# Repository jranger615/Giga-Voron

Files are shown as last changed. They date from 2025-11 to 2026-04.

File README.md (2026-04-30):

# Giga-Voron

#### 4-25-2026 - adding LOW version of my Adapter, this lowers the mount by 10mm (Raises the voron), which should allow for use of the stock connection cable. I HAVE not tested it out but it should work fine, just make sure to keep your stock stepper Z min position if you use it. 

## Things you may want to buy
* To save some assembly steps and the need for buy tons of screws you can by a fully assembled stealth burner. It will require dissassembly to attach to the new mounts and replace board/wiring
https://www.formbot3d.com/products/stealthburner-extruder-for-troodon-20?VariantsId=11006
* The stock board uses  ZH1.5 Connectors, you can buy connector packs on amazon, for ease of use, i buy the pre-crimped ones as they are tiny.
* 2510 24v Fan (Optional for Extruder Board Cooling)
* Longer Cable for the CAN  XT30 2+2. I extended mine but also made a new model of the mount to raise it up for the stock use. Will need to adjust your Z if you do this
* Some M3 screws for assembly (Various sizes for the LID, LID Fan, and Installing the board and adapter
  
## Things to Print
* Your StealthBurner and Prefered Hot End Assembly (If you dont buy and dissasemble formbot)
* The Adapter of Choice from the STL Folder (Beacon or Stock Sensor) I have no started the beacon config yet)
* Board Adapter, this allows you to install the stock board on the Voron
* LID of Choice, Standard or FAN LID. This is different then stock stealth burner to accommodate the stock board install 

## ASSEMBLY Notes
* You will have to open up the top holes on the adapter a little or just work your M3 screws through them before install on the stealth burner.
* Light and Stock sensor are very tight fit. Install them before your stealthburner
* Screws will be longer then the stock mount screws. Make sure you dont get them too long or the mount might not sit flush

## Stealthburner
Assemble the VORON Stealthburner if you dindt buy the formBot. Remember we use a different LID and Board Adapter.
* Follow the build guide located here. This is a large step, and your toolhead will only function as well as you assemble it, so take your time.
* this video is also helpful https://youtu.be/dOyYvnehLaI?si=HIRMF422sOZMZnhB

## Board Diagram and Adapter Mount
  The board Adapter attaches with 2 M3 screws and the stock board requires a m3 screw and washer to hold secure.
  * Attach all wires before sliding the board into place. Itsa tight fit and goes in on an angle.
  * There is an allighment pin on the right next to the nut cert, this helps keep the board in place when the 1 bolt is installed
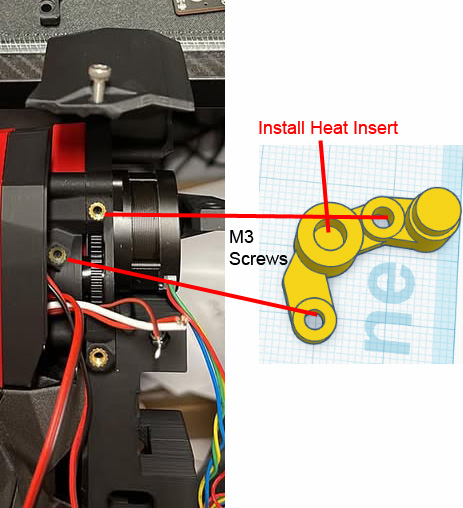
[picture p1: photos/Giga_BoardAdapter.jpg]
  * 
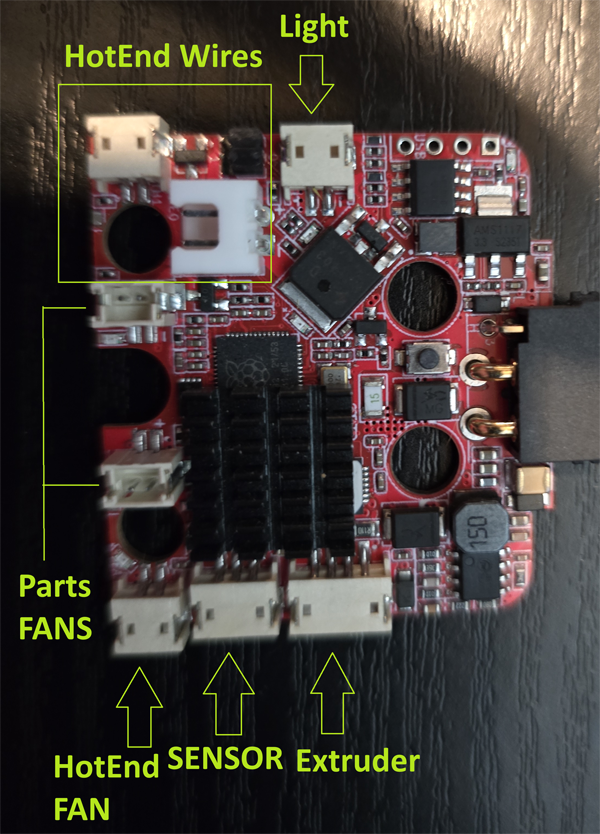
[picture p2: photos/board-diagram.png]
  * 

## Adapter StealthBurner Mount Assembly
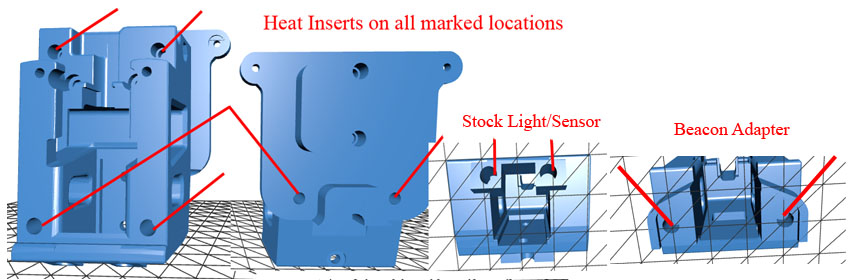
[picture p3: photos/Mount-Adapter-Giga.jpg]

  
## FormBot Moons Stepper Motor Wiring Ref:
* Blue >  Blue (On Stock Connector)
* Red > Red (On Stock Connector)
* Orange > Black (On Stock Connector)
* Black > Green (On Stock Connector)

## Fans:
You can use the Stock Fans from the Giga 
* Bottom fan wire will need to be extended.
* Top Fan, you will have to split the casing apart to fit in the Voron
* Optional 2510 Fan for the Board Cooling Funtion

## Can Bus Wiring XT30 2+2
*  Can Low - Green
*  Can High - Black
*  24V - Red
*  Ground - White

# PRINTER.CFG CHANGES
Y Offset changes everywhere to +15 to accomdate the size of the VORON

## In Probe Offsets
  ```ruby
y_offset: 16
x_offset: 0
z_offset: 10.0      # ← Add +10 (or start with +9.5 and fine-tune)
 ```

## In [stepper_y]
```ruby
 position_min: 29  # Nozzle was more forward then stock and the case was 15 mm bigger. After testing 29 brings the nozzle to the front 
 ```

## In [bed_mesh]
```ruby
 mesh_min:10,45
 ```

## In [gcode_macro CANCEL_PRINT]
  ```ruby
{% set y_park = params.Y|default(printer.toolhead.axis_minimum.y + 45)|int %}   # changed +30 → +45
 ```

## In [gcode_macro PAUSE]
  ```ruby
{% set y_park = params.Y|default(printer.toolhead.axis_minimum.y + 45)|int %}   # changed +30 → +45
 ```

## In [homing_override]
  ```ruby
    {% set y_park = 218 | float %}     # was 203 → add +15
 ```

## In [stepper_z]
  ```ruby
position_min: -22      # ← Change from -12 to -22 (gives more negative room)
 ```

## In [stepper_x]
  ```ruby
position_min: -1     # ← Change from -5 to -1 Position the nozzle at edge 
 ```

## in PLR.CFG
  ```ruby
[delayed_gcode KINEMATIC_POSITION]
initial_duration:0.2
gcode:
      SET_KINEMATIC_POSITION X=0
      SET_KINEMATIC_POSITION Y=25 #Changed from 0 to make sure we dont crash into the front
      SET_KINEMATIC_POSITION Z=0
 ```

## In znp_thr1.cfg (Which ever port you use for yours)
* gear_ratio: 50:10
* rotation_distance: 22.635 #This needs to be adjusted and Calibrated to youyr machine.  Stock start point 22.68 
* sensor_type: ATC Semitec 104NT-4-R025H42G # Change to match Sensor

## Orca Slicer Changes (Specific to Bambu Labs X1C Hotend)
* In the Machine Settings, Set Extruder 1, Retraction length to 1.1
* Layer Heights Limits, Set Max to .48

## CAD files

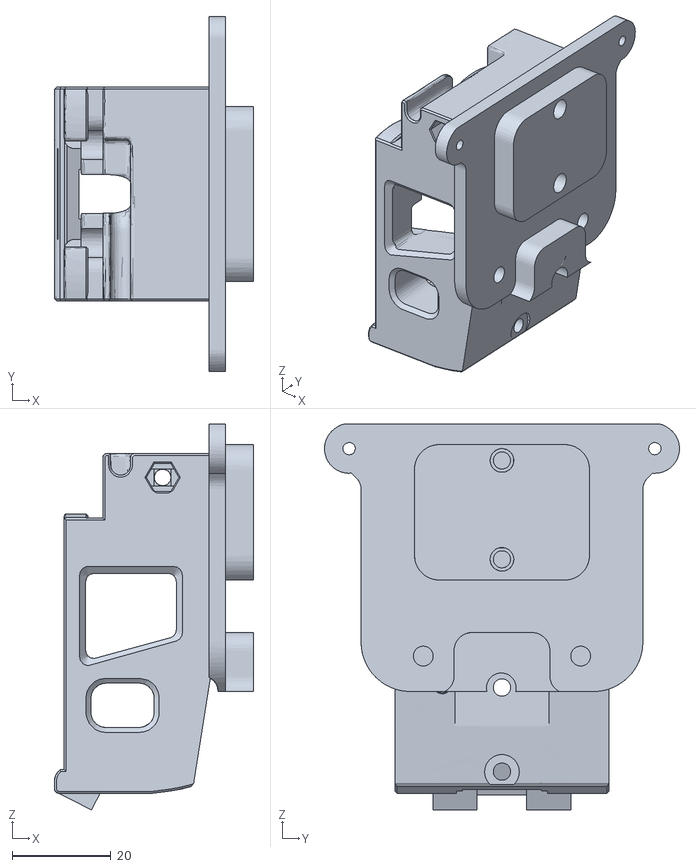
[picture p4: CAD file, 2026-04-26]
STLs/LOW-Giga Voron Stock Adapter.stl
40.3 x 71.8 x 78.1

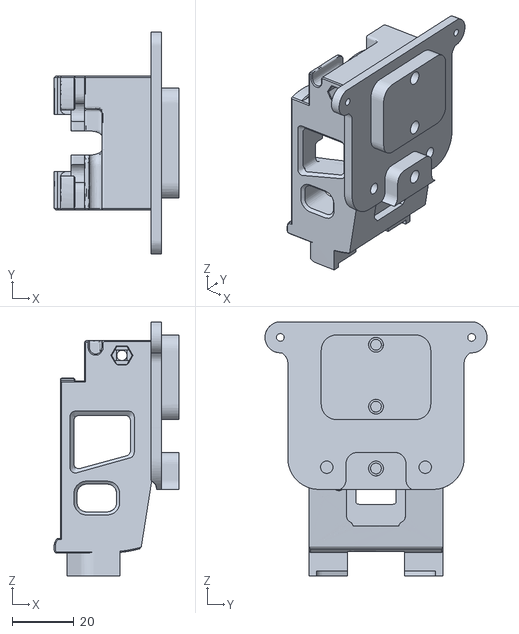
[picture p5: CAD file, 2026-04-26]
STLs/LOW-Giga Voron Beacon Adapter.stl
40.3 x 71.8 x 82.1

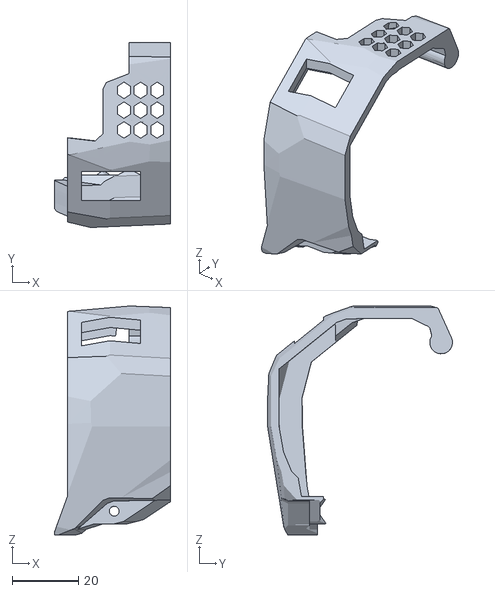
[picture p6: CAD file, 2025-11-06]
STLs/Giga Voron Lid.stl
35.2 x 56.1 x 69.4

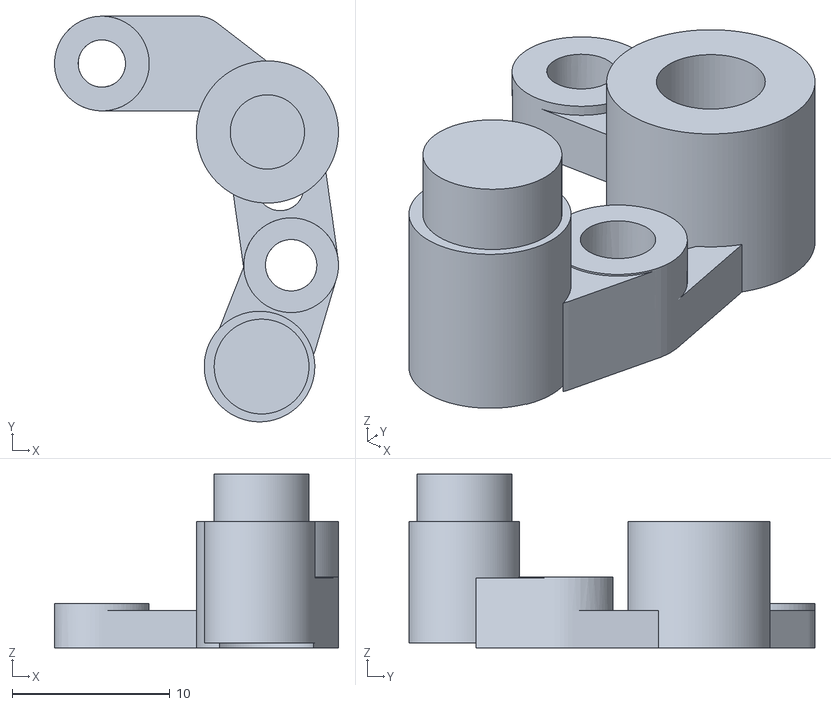
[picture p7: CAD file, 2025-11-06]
STLs/Giga Voron Board Adapter.stl
18.0 x 25.7 x 11.0

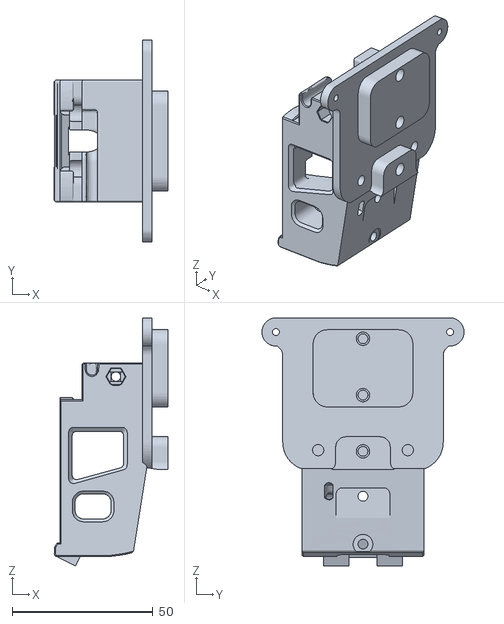
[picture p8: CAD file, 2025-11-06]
STLs/Giga Voron Stock Sensor Adapter.stl
40.3 x 71.8 x 88.1

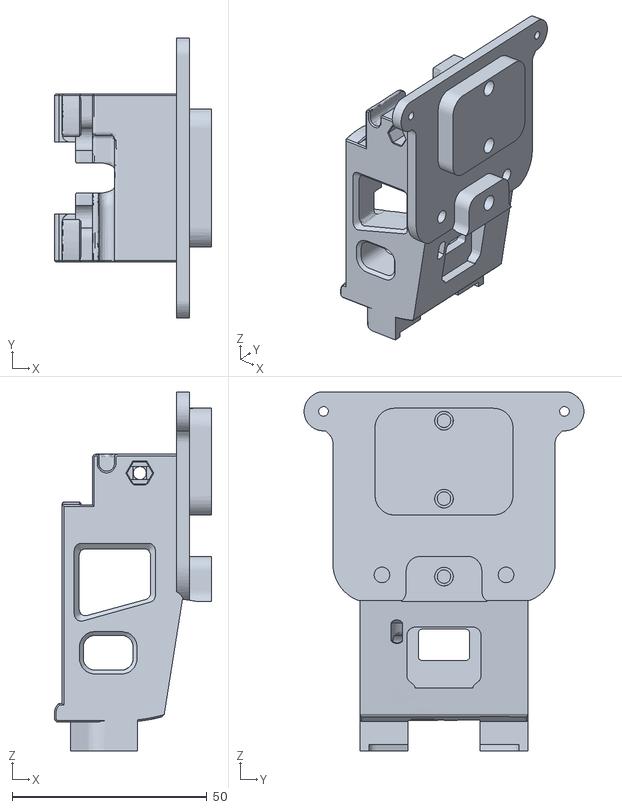
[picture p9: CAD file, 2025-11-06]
STLs/Giga Voron Beacon Adapter.stl
40.3 x 71.8 x 92.1

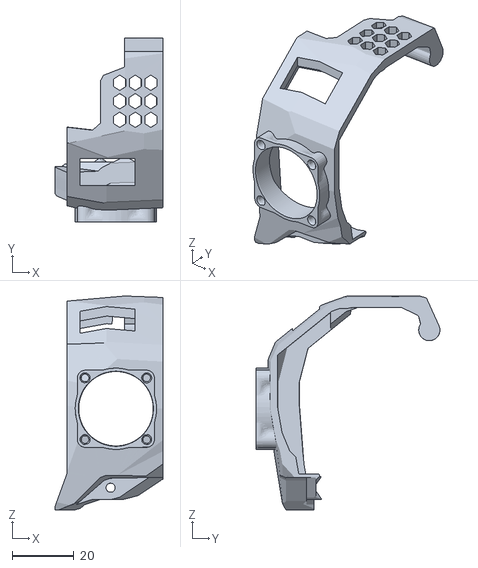
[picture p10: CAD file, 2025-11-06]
STLs/Giga Voron Fan Lid.stl
35.2 x 59.6 x 69.4

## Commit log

2025-11-06 Rename Giga Voron Beacon Adapter.stl to STLs/Giga Voron Beacon Adapter.stl
    [Giga Voron Beacon Adapter.stl]
2025-11-06 Rename Giga Voron Board Adapter.stl to STLs/Giga Voron Board Adapter.stl
    [Giga Voron Board Adapter.stl]
2025-11-06 Rename Giga Voron Fan Lid.stl to STLs/Giga Voron Fan Lid.stl
    [Giga Voron Fan Lid.stl]
2025-11-06 Rename Giga Voron Lid.stl to STLs/Giga Voron Lid.stl
    [Giga Voron Lid.stl]
2025-11-06 Rename Giga Voron Stock Sensor Adapter.stl to STLs/Giga Voron Stock Sensor Adapter.stl
    [Giga Voron Stock Sensor Adapter.stl]
2026-04-22 Update README with assembly and wiring instructions
    Added detailed instructions for assembly and wiring of the stealth burner and fans.
2026-04-23 Update README with connector and wiring details
    Added information about ZH1.5 connectors and wiring for stepper motors.
2026-04-23 Update README with fan and connector details
2026-04-25 Update Can Bus Wiring section title in README
2026-04-25 Add probe offsets section to README
2026-04-25 Add stepper_y section to README
2026-04-25 Fix formatting in README.md for stepper_y and bed_mesh
2026-04-25 Update README with cooling fan configuration details
    Added instructions for modifying the cooling fan settings in the gcode_macro M106 section.
2026-04-25 Clean up fan control code in README
    Removed commented-out sections for clarity.
2026-04-25 Update README with PRINT_START macro details
    Added gcode_macro PRINT_START to manage fan settings for multiple prints.
2026-04-25 Enhance README with extruder fan macro details
    Updated README to include new gcode_macro for extruder fan control and removed Fan1 functions from M106.
2026-04-25 Update README to improve extruder fan instructions
    Clarify the comment for the extruder fan command.
2026-04-25 Remove extruder board cooler details from README
    Removed extruder board cooler section and related macros from README.
2026-04-25 Revise configuration section in README
    Updated configuration parameters for clarity and added notes for calibration.
2026-04-25 Fix typo in README regarding Top Fan installation
2026-04-26 Revise adapter note for clarity and formatting
    Updated header formatting and clarified connection cable usage.
2026-04-26 Rename LOW-Giga Voron Board Adapter.stl to LOW-Giga Voron Stock Adapter.stl
    [LOW-Giga Voron Stock Adapter.stl]
2026-04-26 Update README with stepper_x position_min change
    Added section for stepper_x configuration with updated position_min.
2026-04-26 Fix wiring color descriptions in README.md
2026-04-26 Update README with LID options and assembly notes
    Added information about LID options and assembly notes for the stealth burner installation.
2026-04-28 Update README with Stealthburner assembly instructions
    Added instructions for assembling the Stealthburner and referenced a helpful video.
2026-04-30 Add Board Diagram and Adapter Mount section
    Added a section for the Board Diagram and Adapter Mount with instructions and images.
